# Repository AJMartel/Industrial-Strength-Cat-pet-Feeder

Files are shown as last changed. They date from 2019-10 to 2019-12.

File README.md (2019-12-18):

# Source Code for Industrial Strength Cat Feeder

This is the source code for the Industrial Strength Cat Feeder
https://www.youtube.com/watch?v=O389UU_VG1o

You can find the instructions to build this project on instructables at:
https://www.instructables.com/id/Industrial-Strength-Cat-pet-Feeder/

You can find the 3d printing files on thingiverse at:
https://www.thingiverse.com/thing:3869594

## This project source files belong in two directories on your pi

The two directories are: /vaw/www/html && /home/icf/catFeeder

## download the files to the directories on your pi

## What the feeder does
The industrial Strength Cat Feeder is a pet feeder project which is web/internet based:
Computer (raspberry pi) controlled 
Operated by web server
Web server displays current photo of bowl
Web server has buttons to: feed on demand, take new photo, easily customize automatic feeding times, indicate how much food has been dispensed 
Feed Various amounts of kibble at various times of day - easily customized
Emails photos before and after feeding to verify operation
Take picture on demand
Web server displays current photo of bowl on web site

This feeder is actually designed as a subpart for an outdoor feral cat feeding system. The outdoor feeding system contains two of these feeders for redundancy in case of a failure.The outdoor system is raccoon proof. It is designed to be operated unattended for long periods of time. I will link the larger outdoor system at a later date.

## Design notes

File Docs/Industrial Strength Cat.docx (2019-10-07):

# Industrial Strength Cat (pet) Feeder

By jplanaux (https://www.instructables.com/member/jplanaux/) in Circuits (https://www.instructables.com/circuits/)Raspberry Pi (https://www.instructables.com/circuits/raspberry-pi/projects/)

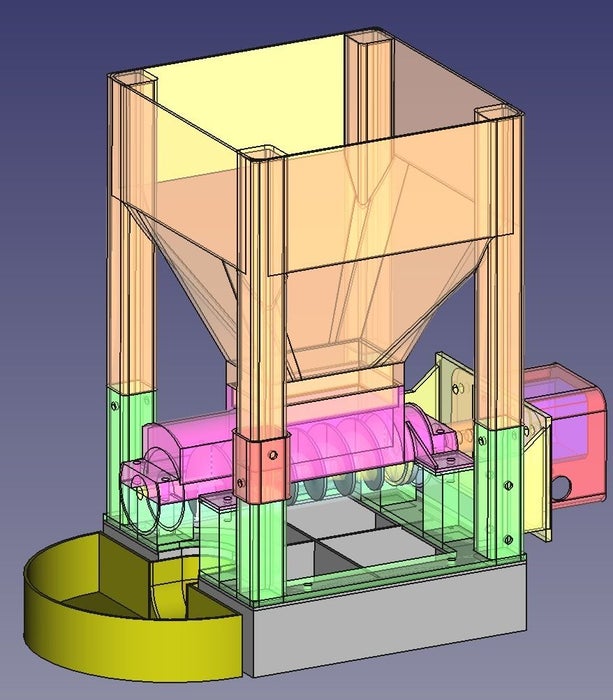
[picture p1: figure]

I travel for many weeks at a time and I have these outdoor feral cats that need to be fed while I am away. For several years, I have been using modified feeders purchased from Amazon that are controlled using a raspberry pi computer. Even though my feeding system uses two feeders (primary and backup), reliability of the residential grade feeders has been a concern. This project removes a lot of the reliability concern. This feeder is superior to the modified purchased feeders in the following ways: Easier to program, IOT, heavy duty motor, bearings on shaft. Moving parts are all steel, dispenses all food (none left in feeder), disassembly is easy, allows thorough cleaning, and feed rate is consistent full or near empty.

The industrial Strength Cat Feeder is a pet feeder project which is web/internet based: Computer (raspberry pi) controlled.

The feeder is operated by a web server. The server displays the current photo of bowl. The web server has buttons to: feed on demand, take new photo, easily customize automatic feeding times, indicate how much food has been dispensed Feed Various amounts of kibble at various times of day - easily customized Emails photos before and after feeding to verify operation Take picture on demand Web server displays current photo of bowl on web site Logs and displays how much food has been dispensed.

Reliability - High quality motor, bearings to minimize wear, battery backup for pi.

Connectivity - Away from the home? Check on your pet’s food supply.

This feeder is actually designed as a subpart for an outdoor feral cat feeding system. The outdoor feeding system contains two of these feeders for redundancy in case of a failure. The outdoor system is raccoon proof. It is designed to be operated unattended for long periods of time. I will link the larger outdoor system at a later date.

Because others may want to use this feeder in an indoor environment, I added a base, cover and bowl. I will be using mine without the base and bowl. I also include an extension in case someone wants extra capacity.

I have been using raspberry pi controlled feeders for extended periods of time and I am satisfied with the reliability. This feeder has been in operation for a few weeks, been disassembled and inspected. The feeder was easily disassembled and cleaned up easy. I could remove all remnants of food to keep my animals from getting sick. I believe that the reliability will be very high.

This project requires a 3d printer. This should not be a problem if you don't have one and live in a large metro area. Many libraries have 3d printers now.

Disclaimer: This project links to other web sites that cover the necessary steps to install software on a raspberry pi, etc. This is my first "instructable", and these instructions are written at a high level and do not get into the smallest of details. Some further investigation/research may be required.

### Supplies:

Logic Level Converter
(https://www.amazon.com/gp/product/B07LG646VS/ref=ppx_yo_dt_b_asin_title_o03_s00?ie=UTF8&psc=1)Raspberry Pi
(https://www.amazon.com/Raspberry-Pi-Model-Motherboard-Element/dp/B07CTF2GWR?rnid=2528832011&s=electronics)Raspberry Pi Micro USB Power Supply (https://www.amazon.com/gp/product/B00GF9T3I0/ref=ppx_yo_dt_b_asin_title_o04_s00?ie=UTF8&psc=1)

Relay (https://www.amazon.com/gp/product/B00LW15F42/ref=ppx_yo_dt_b_asin_title_o04_s00?ie=UTF8&psc=1)

Brass Threaded Inserts
(https://www.amazon.com/gp/product/B07L96KVP3/ref=ppx_yo_dt_b_asin_title_o09_s00?ie=UTF8&psc=1)DC Power Supply (https://www.amazon.com/gp/product/B06Y64QLBM/ref=ppx_yo_dt_b_asin_title_o01_s00?ie=UTF8&psc=1)

Stepper Motor Driver
(https://www.amazon.com/gp/product/B07HHS14VQ/ref=ppx_yo_dt_b_asin_title_o01_s00?ie=UTF8&psc=1)Rubber Sealed Ball Bearing
(https://www.amazon.com/gp/product/B07FGVFN6F/ref=ppx_yo_dt_b_asin_title_o02_s01?ie=UTF8&psc=1)Stepper Motor (https://www.amazon.com/gp/product/B00PNEQKC0/ref=ppx_yo_dt_b_asin_title_o04_s01?ie=UTF8&psc=1)

Flexible Coupling
(https://www.amazon.com/gp/product/B01HBPHSII/ref=ppx_yo_dt_b_asin_title_o04_s01?ie=UTF8&psc=1)SD Card

USB Camera (https://www.amazon.com/gp/product/B008GWPC1Q/ref=ppx_yo_dt_b_search_asin_title?ie=UTF8&psc=1)

8mm Flange Shaft Coupling (https://www.amazon.com/gp/product/B07FLTKK8B/ref=ppx_yo_dt_b_asin_title_o07_s00?ie=UTF8&psc=1)

8mm x 100mm Metal Round Shaft (https://www.amazon.com/gp/product/B076XVKMYK/ref=ppx_yo_dt_b_asin_title_o07_s00?ie=UTF8&psc=1)

## Step 1: Understanding How the Feeder Works

The feeder consists of a hopper which holds food. The hopper sits on top of a screw conveyor. The screw conveyor is turned by a stepper motor which has more than enough torque to turn the auger.

The motor is driven by a 12V transformer through a stepper controller. The power to the controller is controlled by a relay which turns the power on/off only when the feeder is operating. Stepper motors use power even when they are not turning. This is why I installed a relay - only supply power when the motor is required. The stepper controller is controlled by a raspberry pi computer which has a web server.

The web server index page has four buttons which control the pi. There is a "settings" button (linked to a settings page), "feed now" button (linked to a feed now page), "picture" button (linked to a picture page), and a "reset fill" (linked to a reset page).

"Settings button" -> settings.php - this page writes the settings to a text file(configuration.txt) located in the /var/www/html directory. This txt file will be read every hour to see if it is time to feed and how much to feed.

"Feed Now" -> button.php - this page calls the shell script "feedNow.sh" which calls the python script “/home/icf/catFeeder/feedNow.py".

"Reset button" just resets the feeder count to zero. The current count is maintained by the file "fdrCount.txt".

"Picture button" forces the camera to take a new picture. The picture on the web site is updated once an hour and is taken 10 minutes after every hour (after the feeder has dispensed the food.

The crontab will be modified to run a python script "checkDispenseFood.py" every hour on the hour. This script reads the configuration.txt file. It looks at the current time, sees if the times match for any of the three feed times. If there is a match, it dispenses the amount of food that is set by the configuration.txt file. The script also calls a script which emails a photo from the camera before feeding and after feeding. This way someone can verify that they are eating all of the food and that the dispenser is actually working.

The auger has been tested with only one type of cat kibble (Meow Mix). The feeder does empty the hopper completely with very little "rat holing". The feeder appears to dispense consistent amounts of food whether the hopper is completely full or near empty.

## Step 2: Start Printing the Cat Feeder Parts and Order the Parts to Purchase

All of the 3d printer files are located at thingiverse. Link
(https://www.thingiverse.com/thing:3869594)

Download and start printing all of the stl files. They will take a while to print, so while all of the parts are printing, move onto the computer part of the project.

## Step 3: Start Loading OS on the Pi and Configure

These instructions are for a headless install. I use a mac so I don't know if any of the steps will be different on whatever computer type you are using.

Download Raspbian (https://www.raspberrypi.org/downloads/raspbian/)Do not use NOOBS.

Configure and install Raspbian on the sdcard - and install the card in the PI. Instruction Link (https://gallaugher.com/makersnack-setup-a-raspberry-pi-without-a-keyboard-or-mouse-headless-install/). I used balenaEtcher (https://www.balena.io/etcher/).

Install the card and ssh into the pi

Secure your pi (https://blog.robertelder.org/securing-a-raspberry-pi/)

Create the icf (inddustrial Cat Feeder Account)

sudo adduser icf

Install and configure web server - install and configure php (https://www.raspberrypi.org/documentation/remote-access/web-server/apache.md)

Download the files from github (https://github.com/jplanaux/jplanaux.github.io)

## Step 4: Copy the Web Server Files Over to the /var/www/html Folder

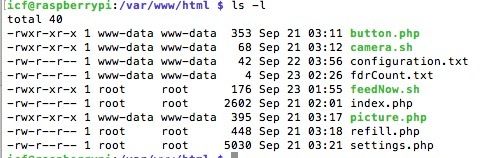
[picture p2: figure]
Picture of Copy the Web Server Files Over to the /var/www/html Folder

Copy the web server files over to the /var/www/html folder

Verify/set the Permissions/owners of the Files

After the files are copied on the pi, verify that the owners and permissions match the image.

If you are new to linux/raspberry pi? Google "chown" & "chmod" to learn how to set owner and permission in Linux.

## Step 5: Modify the 'sudoers' File

Type in the following command<br><em>sudo nano /etc/sudoer </em>

Add the line to the bottom of the file

www-data ALL=(ALL) NOPASSWD: /var/www/html/feedNow.sh, NOPASSWD : /var/www/html/camera.sh

## Step 6: Copy the Script Files to the CatFeeder Directory

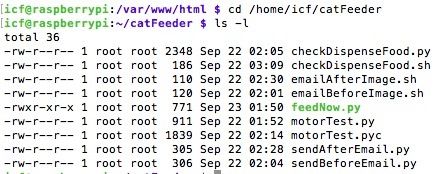
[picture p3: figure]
Picture of Copy the Script Files to the CatFeeder Directory

Create a catFeeder directory in the icf directory and copy the files from github into that directory.

Check and set the owners/permissions so that they match the image above.

Change the code in the following files for your email: sendAfterEmail.py, sendBeforeEmail.py

## Step 7: Modify the Crontab File to Run the 'checkDispenseFood' Script

Type in the following at the command line

sudo crontab -e

Add the following line to the bottom of the file

10 */1 * * * sh /home/icf/catFeeder/camera.sh >> /home/icf/logs/camera 2>&1

0 * * * * sh /home/icf/catFeeder/checkDispenseFood.sh >> /home/icf/logs/cronlog

This will execute the 'checkDispenseFood.sh' script every hour on the hour. If the settings from the web server match, the feeder will dispense food.

This will take a picture every 10 minutes after the hour.

## Step 8: Start the Wiring Part of the Project - Build the Control Box

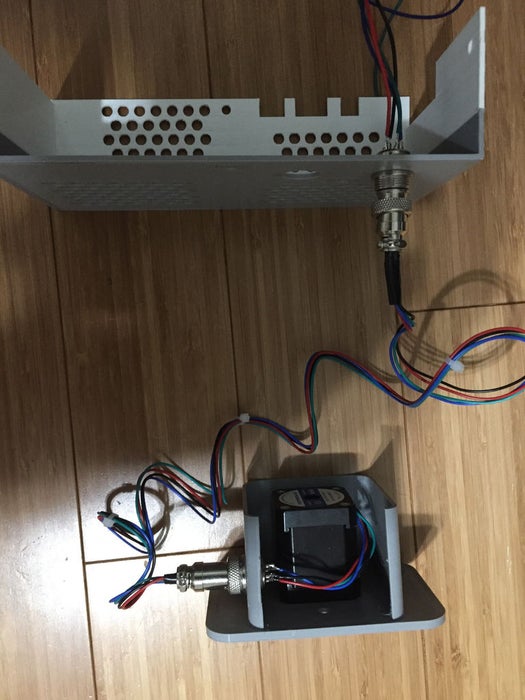
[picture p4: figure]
Picture of Start the Wiring Part of the Project - Build the Control Box
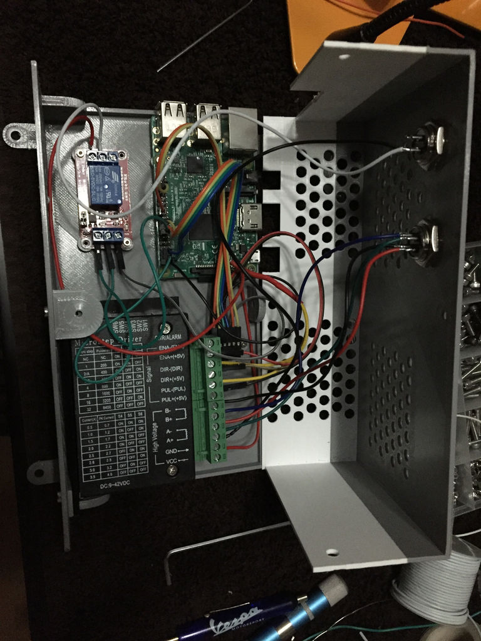
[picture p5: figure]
Picture of Start the Wiring Part of the Project - Build the Control Box

Build the control box. I made my control box large, just so it would make it easier to assemble and wire. I may modify this design and make it much more compact.

Connecting the motor to the control box: Use two aviation plug assemblies. Snip the four (4) wires from the motor. There is one hole in the motor mount for a plug. There are two holes in the control box. Use either hole for the motor plug. Install the motor in the motor mount using (4) four 3mm x 8mm hex sockets and solder the 4 wires to one plug. Snip the dupont connectors off of the other side of the 4 wires and solder the plugs on both sides to make a cable that plugs into the control box. Solder 4 wires to another plug to be used for the control box plug. Install plug in control box

Install the pi using 2 mm X 8 mm hex sockets, relay using 2 mm X 8 mm hex sockets, and controller using M3 x 8 mm and nuts in the box and wire it up per the wiring diagram. Set the controller's dip switches to on, on, off, on, off, off. This project used a combination of dupont wires, regular wires. Some soldering is required. The soldering is mainly required for the plugs. I used the aviation plugs so I can easily plug and unplug.

Snip the end of the transformer wire and solder on another aviation plug. Wire up the power per the wiring diagram.

#### Attachments

- wiring diagram.pdf (https://cdn.instructables.com/ORIG/FIE/E8F5/K10ZIC54/FIEE8F5K10ZIC54.pdf)

## Step 9: Assemble the Cat Feeder

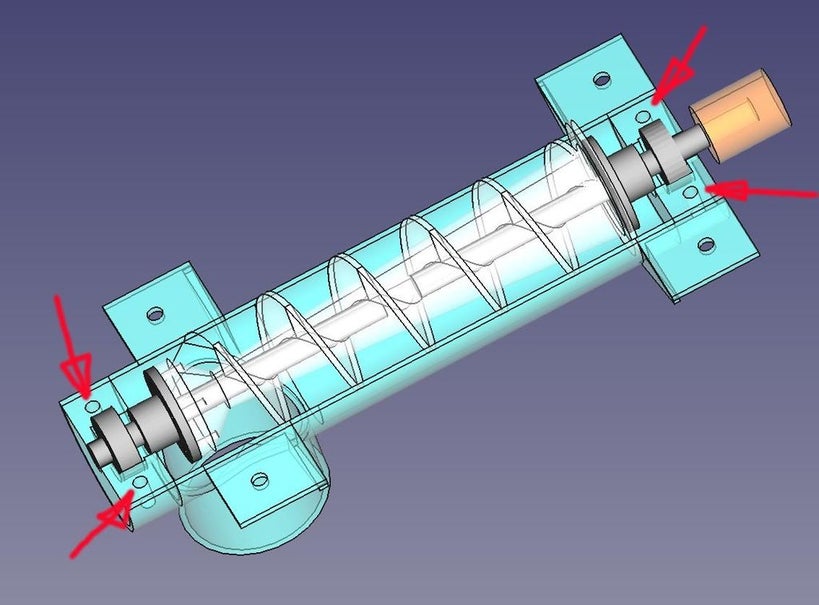
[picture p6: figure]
Picture of Assemble the Cat Feeder
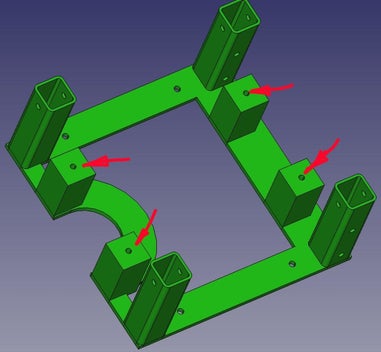
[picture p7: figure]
Picture of Assemble the Cat Feeder
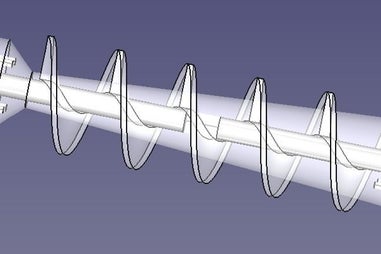
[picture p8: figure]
Picture of Assemble the Cat Feeder

By now, all of your parts should be printed.

Bolting: I used brass inserts for eight connections. I will be cleaning the feeder often, so I need the thread to be in good shape. Insert the brass fittings in the base and the lower housing of the screw feeder.

Assemble the auger - Use a round file if the shafts don't fit inside the auger (I actually had to run a drill through the center and then used a round file to end up with a tight connection). Use 3mm x 8mm cap screws for the end flanges. The shafts should be able to slide in and out the flanges. Make final shaft adjustments during final assembly.

Bolt the base on to the base extension. My actually feeder does not use this. I added the base extension for anyone who builds this that uses a bowl. Use (4) 4mm x 12mm and nuts.

Bolt the Motor support to the motor mount. Use (3) 4mm x 12mm and nuts.

Bolt The Motor support to the base. Use (4) 4mm x 40mm bolts and nuts.

Attach the coupling to the motor shaft.

Slide the bearings onto the auger shaft.

Place the auger in the bottom trough and slide the trough in place, while guiding the shaft into the coupling. Finalize the shaft projections and tighten down all of the set screws associated with the shaft and couplings.

Place the top trough over the bottom trough and bolt down to the base and lower trough.

Add the four splice connectors to the columns and fasten using (4) 4mm x 40mm and nuts.

Add the hopper and bolt the splices to the hopper.

## Step 10: Add Power to the Pi and Control Box

Plug in your pi and your control box. Open up a web browser. Navigate to your pi, set up your feeder times and introduce your cat to its new feeder.

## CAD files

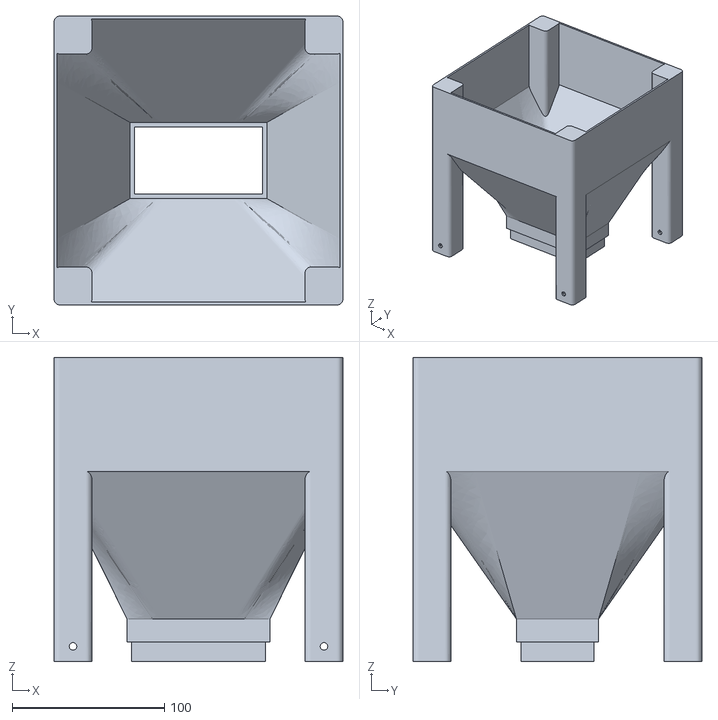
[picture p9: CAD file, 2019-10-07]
STLs/hopper.stl
190.0 x 190.0 x 200.0

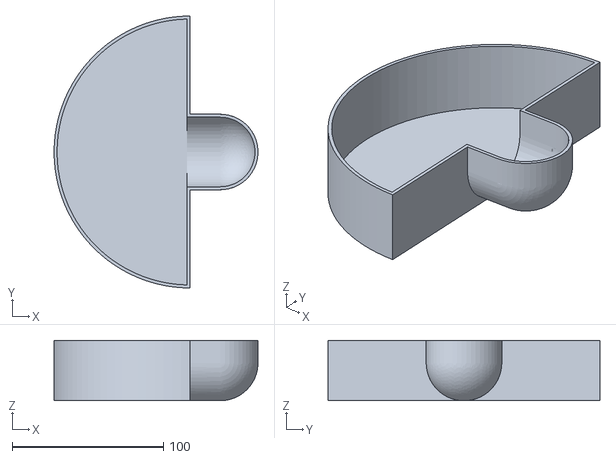
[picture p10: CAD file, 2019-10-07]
STLs/bowl.stl
135.0 x 180.0 x 40.0

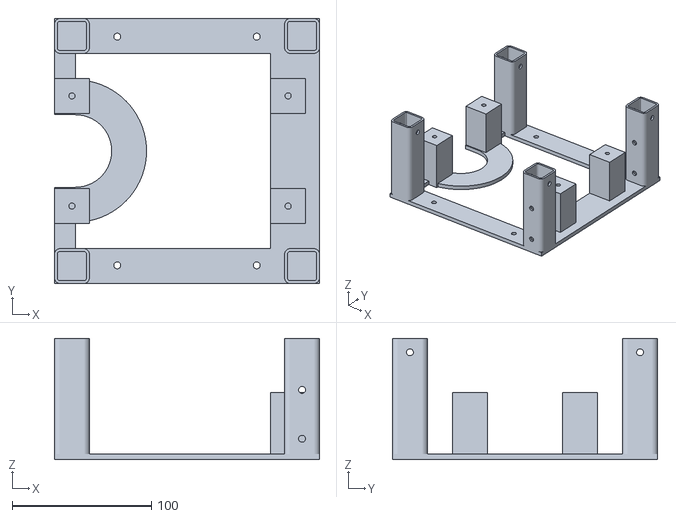
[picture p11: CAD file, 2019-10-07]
STLs/base.stl
190.0 x 190.0 x 87.0

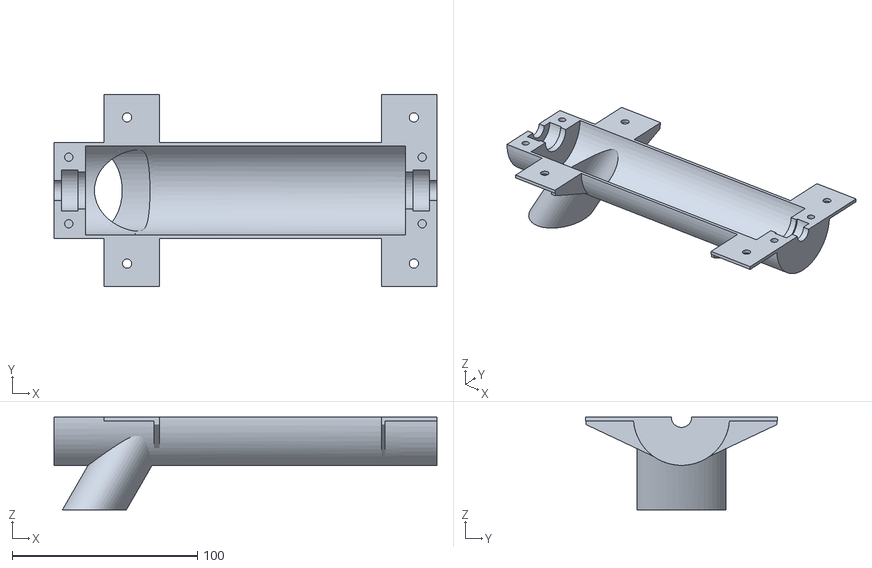
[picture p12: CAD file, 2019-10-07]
STLs/new_trough_bottom.stl
207.0 x 104.0 x 50.0

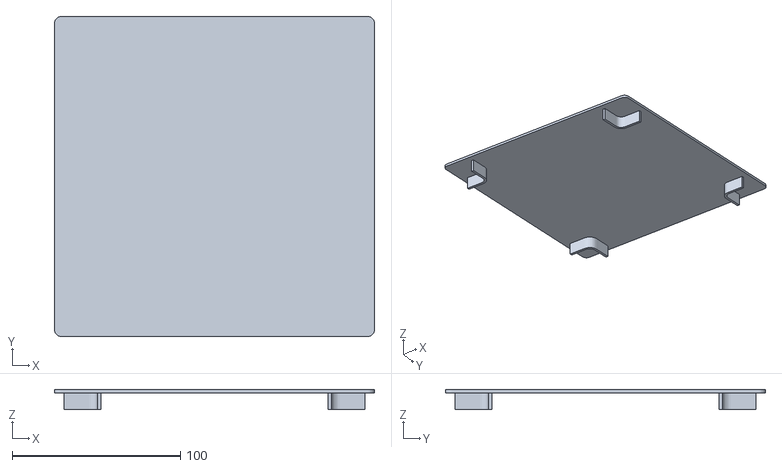
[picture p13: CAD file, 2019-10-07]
STLs/cover.stl
190.0 x 190.0 x 12.0

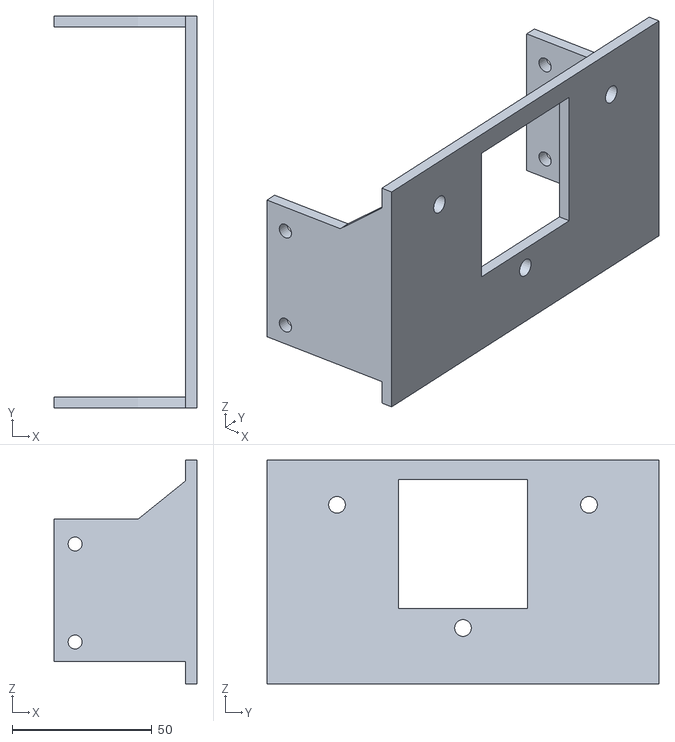
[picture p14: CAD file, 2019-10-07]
STLs/motor_support.stl
51.0 x 140.0 x 80.0

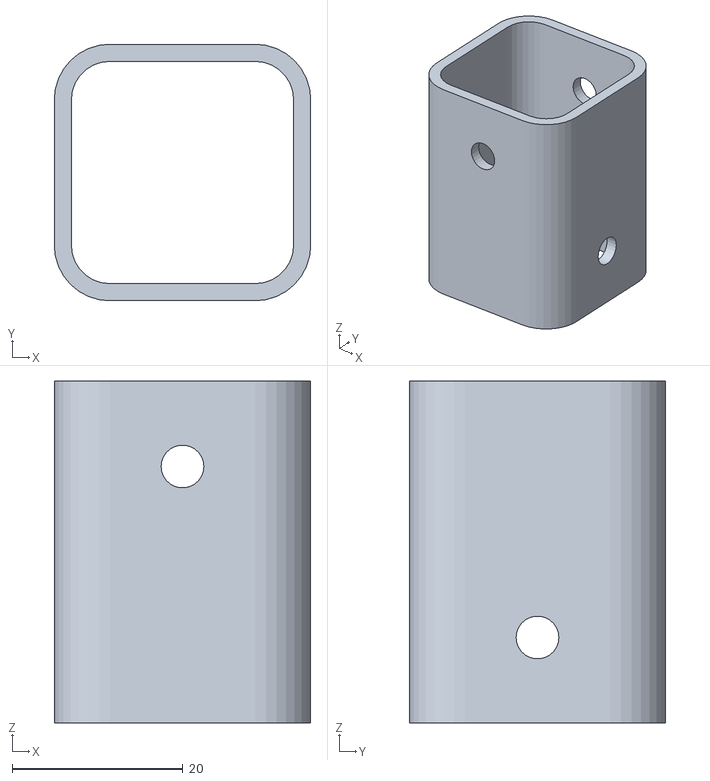
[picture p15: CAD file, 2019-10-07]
STLs/splice.stl
30.0 x 30.0 x 40.0

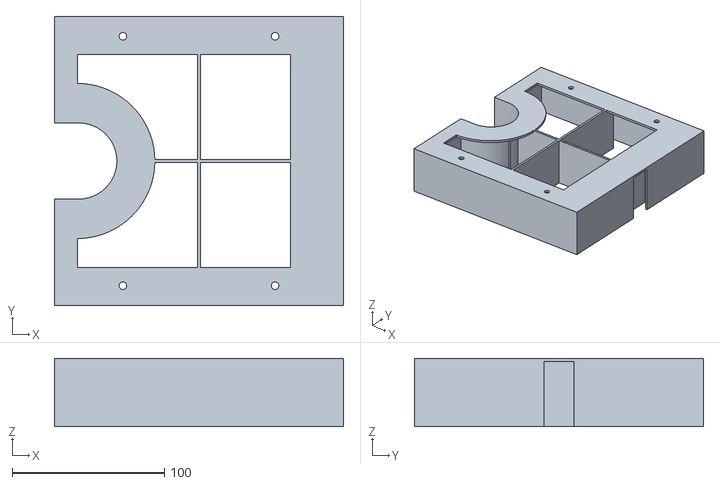
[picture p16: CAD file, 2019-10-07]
STLs/base_platform.stl
190.0 x 190.0 x 45.0

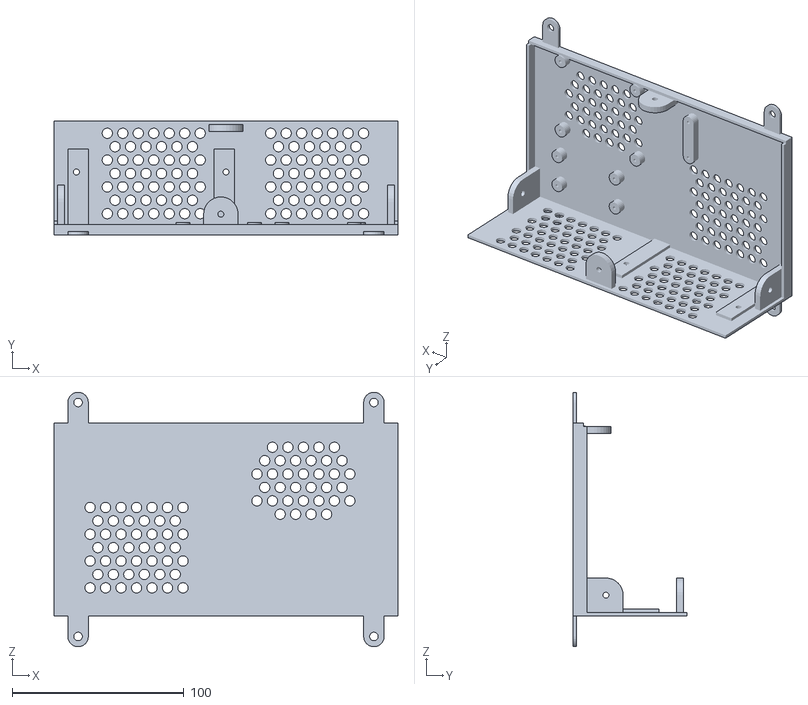
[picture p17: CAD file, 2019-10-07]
STLs/control_box_1.stl
200.0 x 66.0 x 147.9

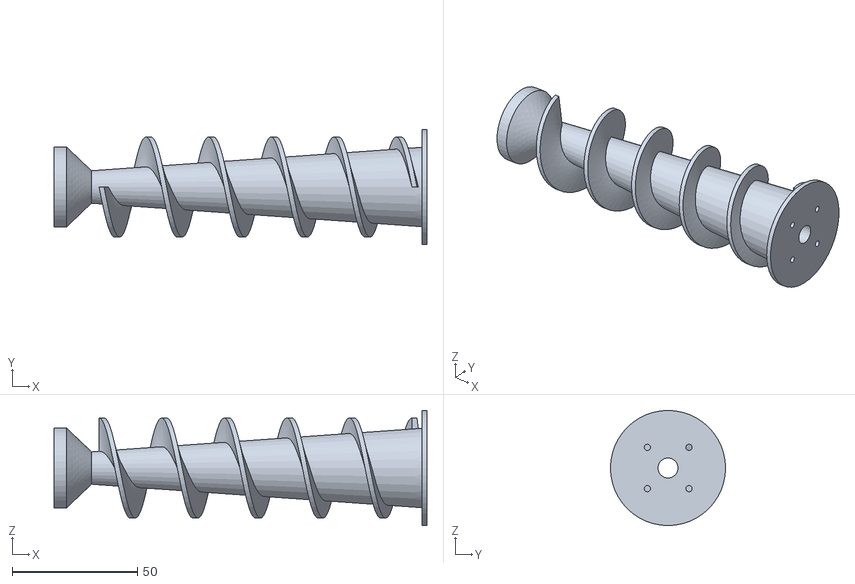
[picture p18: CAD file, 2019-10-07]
STLs/new_auger.stl
149.0 x 46.0 x 46.0

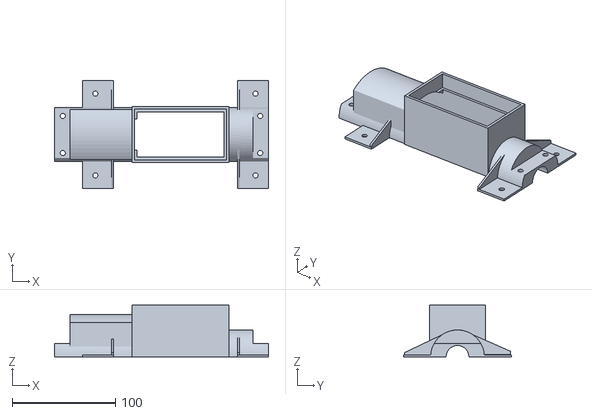
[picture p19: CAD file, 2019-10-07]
STLs/trough_top.stl
207.0 x 104.0 x 50.0

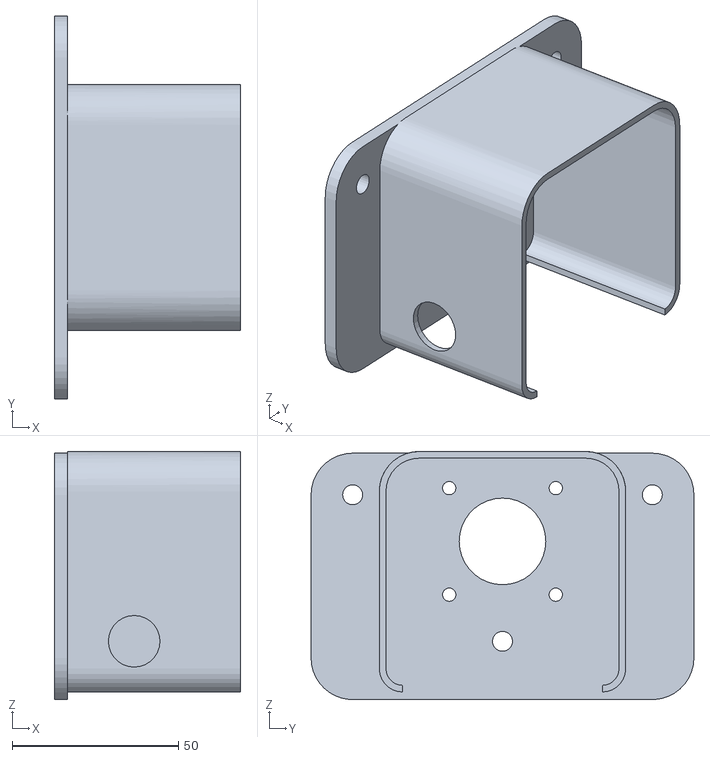
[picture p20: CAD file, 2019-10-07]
STLs/motor_mount.stl
56.0 x 115.0 x 74.5

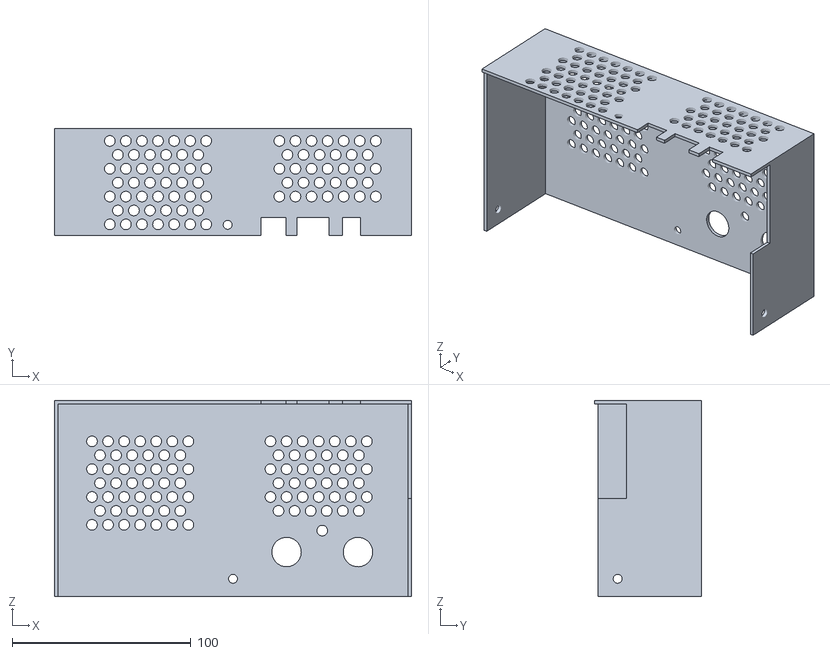
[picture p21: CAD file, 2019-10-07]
STLs/control_box_2.stl
200.0 x 60.0 x 110.0

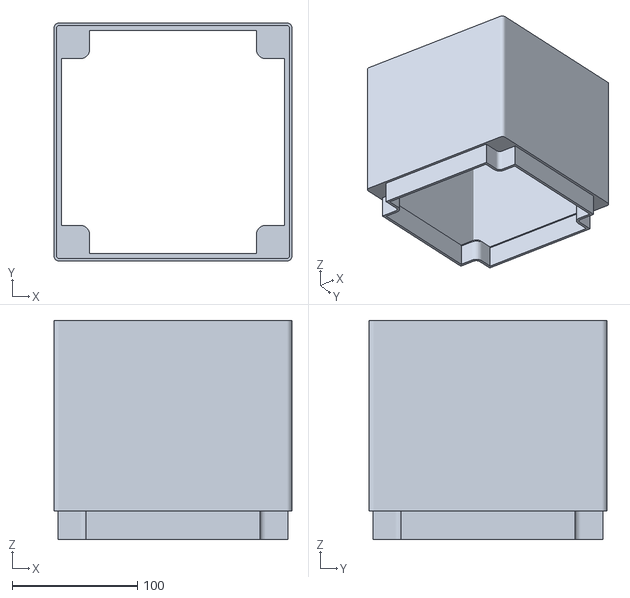
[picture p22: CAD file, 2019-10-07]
STLs/extension.stl
190.0 x 190.0 x 175.0

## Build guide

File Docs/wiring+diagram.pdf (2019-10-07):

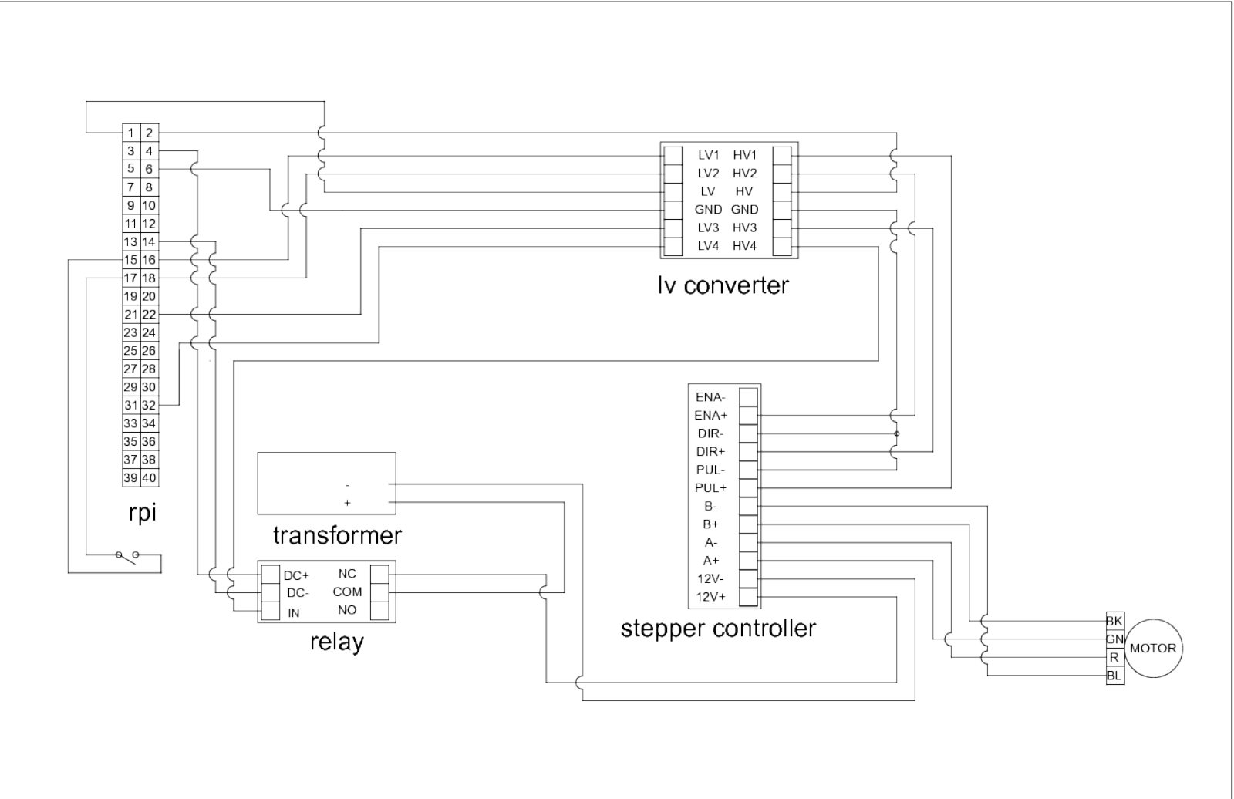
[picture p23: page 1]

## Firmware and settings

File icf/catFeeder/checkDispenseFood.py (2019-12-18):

import time
import motorTest as feederMotor
import subprocess
import datetime
import os

# read the file and assign variables
f = open('/var/www/html/configuration.txt', 'r')
firstFeedTime = f.readline()
print (firstFeedTime)
firstFeedAMPM = f.readline()
firstFeedAmmount = f.readline()
secondFeedTime = f.readline()
secondFeedAMPM = f.readline()
secondFeedAmmount = f.readline()
thirdFeedTime = f.readline()
thirdFeedAMPM = f.readline()
thirdFeedAmmount = f.readline()
f.close()

def updateFdrDispensedQty(amt):
  fileName = os.path.abspath('/var/www/html/fdrCount.txt')
  f= open(fileName, 'r+')
  qty = float(f.readline())
  qty = qty + amt
  f.seek(0)
  f.truncate()
  f.write(str(qty))
  f.close()

def feedAndPhoto():
  subprocess.call("sh /home/icf/catFeeder/emailBeforeImage.sh", shell=True)
  feederMotor.start(str(adjAmt1))
  subprocess.call("sh /home/icf/catFeeder/emailAfterImage.sh", shell=True)

def convertTo24Hour( inputTime, AMPM ):
  if AMPM.strip() == "am":
    returnValue = inputTime.strip()
    if returnValue != 'off':
      return int(returnValue)
    else:
      return returnValue
  else:
    return int(inputTime) + 12

t = time.localtime() # gives you an actual struct_time object
h = t.tm_hour # gives you the hour part as an integer


#compare the local time to each of the feed times
# the feed time could be "off" or a integer value
time1 = convertTo24Hour(firstFeedTime, firstFeedAMPM)
time2 = convertTo24Hour(secondFeedTime, secondFeedAMPM)
time3 = convertTo24Hour(thirdFeedTime, thirdFeedAMPM)


#1072 revolutions = 1 cup of food
#cfMotor.py 
amount1 = float(firstFeedAmmount)
amount2 = float(secondFeedAmmount)
amount3 = float(thirdFeedAmmount)

adjAmt1 = 1072 * amount1
adjAmt2 = 1072 * amount2
adjAmt3 = 1072 * amount3

x = datetime.datetime.now()
print(x)

if firstFeedTime.strip() != 'off' and time1 == h:
  print "First feeding commencing"
  feedAndPhoto()
  updateFdrDispensedQty(amount1)
else:
  print "Not time to feed first"
if secondFeedTime.strip() != 'off' and time2 == h:
  print "Second feeding commencing"
  feedAndPhoto()
  updateFdrDispensedQty(amount2)
else:
  print "Not time to feed second"
if thirdFeedTime.strip() != 'off' and time3 == h:
  print "Third feeding commencing"
  feedAndPhoto()
  updateFdrDispensedQty(amount3)
else:
  print "Not time to feed third"

feederMotor.cleanup()

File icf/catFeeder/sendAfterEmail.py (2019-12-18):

import smtplib
from email.MIMEMultipart import MIMEMultipart
from email.MIMEText import MIMEText
from email.MIMEBase import MIMEBase
from email import encoders

fromaddr = "yourName@yourServer.com"
toaddr = "yourReciepient@server.com"
msg = MIMEMultipart()
msg['From'] = fromaddr
msg['To'] = toaddr
msg['Subject'] = "After Feed"
body = "After Feeding"
msg.attach(MIMEText(body, 'plain'))
filename = "afterImage.jpg"
attachment = open("/home/icf/afterImage.jpg", "rb")
part = MIMEBase('application', 'octet-stream')
part.set_payload((attachment).read())
encoders.encode_base64(part)
part.add_header('Content-Disposition', "attachment; filename= %s" % filename)
msg.attach(part)
server = smtplib.SMTP('smtp.gmail.com', 587)
server.starttls()
server.login("yourUserName", "yourPassword")
text = msg.as_string()
server.sendmail(fromaddr, toaddr, text)
server.quit()
